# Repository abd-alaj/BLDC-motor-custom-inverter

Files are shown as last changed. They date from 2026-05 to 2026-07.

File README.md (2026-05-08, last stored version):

Hello, 

this is the start of our casptone project. 

You will see the following structure (with changes if i have forgotten to update this section):  

```
.
├── data/                    - parameters, csv files, oscilloscope data
├── docs/                    - documentation of our project
├── hardware/                - KiCad Project files, scheamtic, footprints, etc.
│   ├── schematics/             - schematic files
│   ├── layout/                 - PCB layout files
│   ├── libraries/              - custom footprints/symbols
│   └── manufacturing/          - gerbers, BOM, etc.
├── models/                 - main simulink directory
│   └── components/              - smaller components for the model
├── scripts/                 - utility matlab scripts
├── src/                     - C code
└── work/                    - MATLAB throws autogenerated files in here 
```

# How To Use This Code
1. git clone this repo: 
```
git clone https://github.com/abd-alaj/BLDC-motor-custom-inverter.git
```
2. open the `BLDC_motor_custom_inverter.m.prj` file in matlab prior to starting any work.

That's it. This project is in a rather primitive state so this readme file is an active WIP.

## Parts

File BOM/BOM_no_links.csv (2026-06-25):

Reference | Qty | Value | DNP | Exclude from BOM | Exclude from Board | Footprint | Datasheet
C1,C2,C3,C6,C7,C8,C10,C11,C12,C13,C14,C15,C16,C17,C18,C19,C20,C21,C22,C26,C27 | 21 | 100n |  |  |  | Capacitor_SMD:C_0603_1608Metric
C4,C5,C9 | 3 | 4.7u |  |  |  | Capacitor_SMD:C_0603_1608Metric
C28,C29 | 2 | 330u |  |  |  | footprint:PCAP_12_5x20-THRU-ELECT_NCA
C30,C31 | 2 | 1u |  |  |  | Capacitor_SMD:C_0603_1608Metric
C32,C33,C34,C35,C36,C37 | 6 | 10u |  |  |  | Capacitor_SMD:C_0805_2012Metric
CR1,CR3 | 2 | SMCJ26 |  |  |  | footprint:SMCJSeries_LTF | SMCJ26
D1,D2,D3 | 3 | MURA160T3G |  |  |  | footprint:MURA160T3G
D4,D6 | 2 | MM5Z10VT1G |  |  |  | Diode_SMD:D_SOD-523 | https://diotec.com/tl_files/diotec/files/pdf/datasheets/mm5z2v4.pdf
D5 | 1 | SS14 |  |  |  | Diode_SMD:D_SMA | https://www.vishay.com/docs/88746/ss12.pdf
D7,D8,D9,D10 | 4 | LED |  |  |  | LED_SMD:LED_0603_1608Metric
J1 | 1 | Screw_Terminal_01x03 |  |  |  | TerminalBlock_Phoenix:TerminalBlock_Phoenix_MKDS-1,5-3-5.08_1x03_P5.08mm_Horizontal
J2,J3,J4 | 3 | Screw_Terminal_01x02 |  |  |  | TerminalBlock_Phoenix:TerminalBlock_Phoenix_MKDS-1,5-2-5.08_1x02_P5.08mm_Horizontal
J5 | 1 | Conn_01x08_Pin |  |  |  | Connector_JST:JST_XH_B8B-XH-A_1x08_P2.50mm_Vertical
Q1,Q2,Q3,Q4,Q5,Q6 | 6 | IRLZ44N |  |  |  | Package_TO_SOT_THT:TO-220-3_Vertical | http://www.irf.com/product-info/datasheets/data/irlz44n.pdf
Q7,Q9 | 2 | DMP6050SSD |  |  |  | Package_SO:SOIC-8_3.9x4.9mm_P1.27mm | https://www.diodes.com/assets/Datasheets/DMP6050SSD.pdf
R1,R2,R3,R6,R7,R8,R10,R11,R12 | 9 | 10 |  |  |  | Resistor_SMD:R_0603_1608Metric
R4,R17 | 2 | 47k |  |  |  | Resistor_SMD:R_0603_1608Metric
R5,R9,R16 | 3 | 4.7k |  |  |  | Resistor_SMD:R_0603_1608Metric
R13,R14,R15 | 3 | 10m |  |  |  | Resistor_SMD:R_2512_6332Metric
R18,R19,R20,R28 | 4 | 3.3k |  |  |  | Resistor_SMD:R_0603_1608Metric
R21,R22,R30,R31,R32,R33,R34,R35,R36,R37,R38,R39,R40,R41,R42 | 15 | 0 |  |  |  | Resistor_SMD:R_0402_1005Metric
R23,R24,R27 | 3 | 680 |  |  |  | Resistor_SMD:R_0603_1608Metric
R25,R26 | 2 | 10k |  |  |  | Resistor_SMD:R_0603_1608Metric
R29 | 1 | 33k |  |  |  | Resistor_SMD:R_0603_1608Metric
R43 | 1 | 680 |  |  |  | Resistor_SMD:R_0603_1608Metric_Pad0.98x0.95mm_HandSolder
R44 | 1 | 100 |  |  |  | Resistor_SMD:R_0603_1608Metric_Pad0.98x0.95mm_HandSolder
R45 | 1 | 6.98k |  |  |  | Resistor_SMD:R_1206_3216Metric_Pad1.30x1.75mm_HandSolder
R46 | 1 | 3k |  |  |  | Resistor_SMD:R_0805_2012Metric_Pad1.20x1.40mm_HandSolder
RV1 | 1 | 10k |  |  |  | Potentiometer_THT:Potentiometer_Alps_RK09K_Single_Vertical
TP1,TP2,TP3,TP4,TP5,TP6,TP7,TP8,TP9,TP10,TP11,TP12,TP13,TP14,TP15,TP16,TP17,TP18,TP20,TP24 | 20 | TestPoint |  |  |  | TestPoint:TestPoint_Pad_1.5x1.5mm
TP21,TP22,TP23 | 3 | Keystone 5015 |  |  |  | TestPoint:TestPoint_Keystone_5015_Micro_Mini
U1 | 1 | NUCLEO64-F411RE |  |  |  | Module:ST_Morpho_Connector_144_STLink | http://www.st.com/st-web-ui/static/active/en/resource/technical/document/data_brief/DM00105918.pdf
U2,U3,U4 | 3 | INA181 |  |  |  | Package_TO_SOT_SMD:SOT-23-6 | http://www.ti.com/lit/ds/symlink/ina181.pdf
U5,U6,U7 | 3 | ADUM3223ARZ |  |  |  | footprint:SOIC127P600X175-16N
U8 | 1 | LMV321 |  |  |  | footprint:LMV321DBV5 | http://www.ti.com/lit/ds/symlink/lmv324.pdf
U9,U10,U11 | 3 | TL331 |  |  |  | Package_TO_SOT_SMD:SOT-23-5 | http://www.ti.com/lit/ds/symlink/tl331.pdf
U12 | 1 | AP2112K-2.6 |  |  |  | Package_TO_SOT_SMD:SOT-23-5 | https://www.diodes.com/assets/Datasheets/AP2112.pdf
U13 | 1 | 74LVC1G332 |  |  |  | footprint:MURA160T3G | http://www.ti.com/lit/sg/scyt129e/scyt129e.pdf

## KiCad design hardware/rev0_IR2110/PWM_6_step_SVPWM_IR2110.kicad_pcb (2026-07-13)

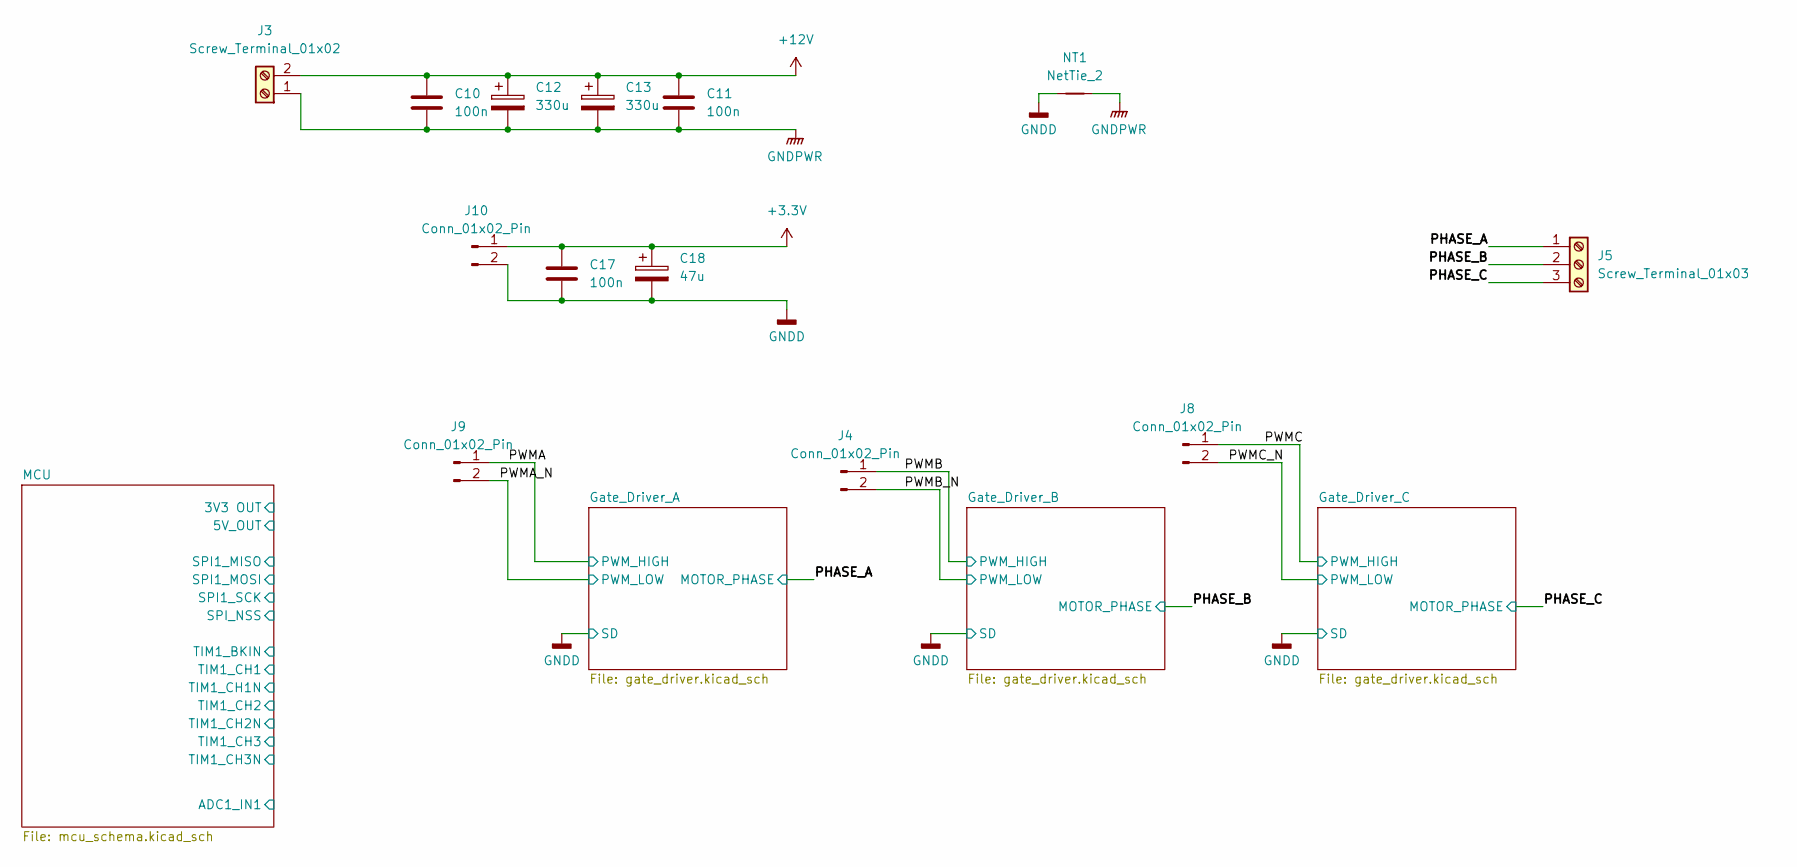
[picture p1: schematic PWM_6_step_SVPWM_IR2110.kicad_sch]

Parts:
C10, C11, C17: 100n; C_1206_3216Metric
C12, C13: 330u; PCAP_12_5x20-THRU-ELECT_NCA
C18: 47u; CP_Radial_D8.0mm_P3.50mm
J3: Screw_Terminal_01x02; TerminalBlock_TE_282834-2_1x02_P2.54mm_Horizontal
J4, J8, J9, J10: Conn_01x02_Pin; PinHeader_1x02_P2.54mm_Vertical
J5: Screw_Terminal_01x03; TerminalBlock_TE_282834-3_1x03_P2.54mm_Horizontal
NT1: NetTie_2; NetTie-2_SMD_Pad2.0mm

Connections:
+3.3V: C17.1, C18.1, J10.1; also elsewhere on the board
+12V: C10.1, C11.1, C12.1, C13.1, J3.2; also elsewhere on the board
/PHASE_A: J5.1; also elsewhere on the board
/PHASE_B: J5.2; also elsewhere on the board
/PHASE_C: J5.3; also elsewhere on the board
/PWMA: J9.1; also elsewhere on the board
/PWMA_N: J9.2; also elsewhere on the board
/PWMB: J4.1; also elsewhere on the board
/PWMB_N: J4.2; also elsewhere on the board
/PWMC: J8.1; also elsewhere on the board
/PWMC_N: J8.2; also elsewhere on the board
GNDD: C17.2, C18.2, J10.2, NT1.1; also elsewhere on the board
GNDPWR: C10.2, C11.2, C12.2, C13.2, J3.1, NT1.2; also elsewhere on the board

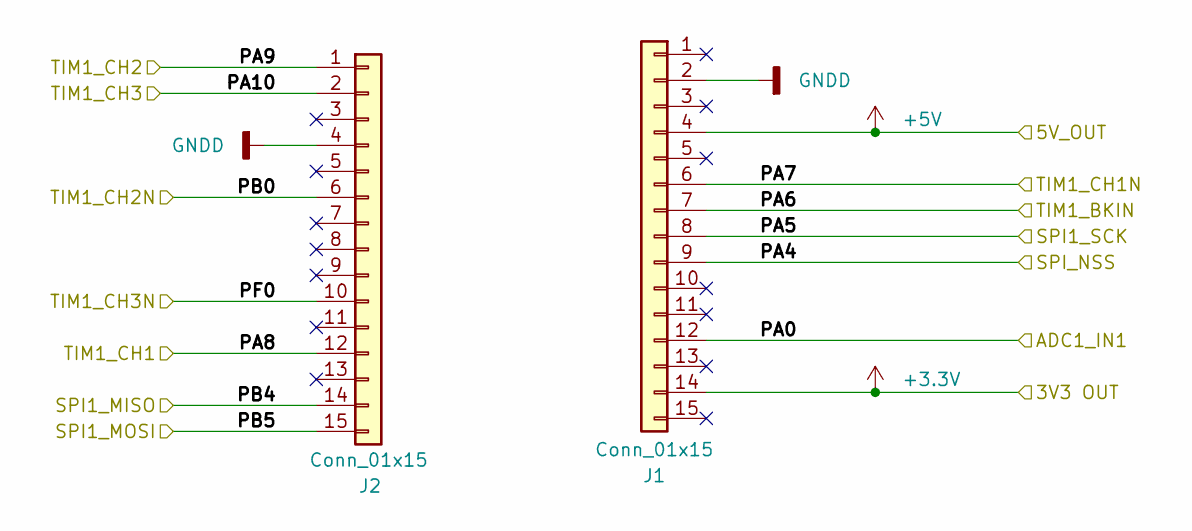
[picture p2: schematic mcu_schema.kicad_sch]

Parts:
J1, J2: Conn_01x15; PinSocket_1x15_P2.54mm_Vertical

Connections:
unnamed: J1.2, J2.4

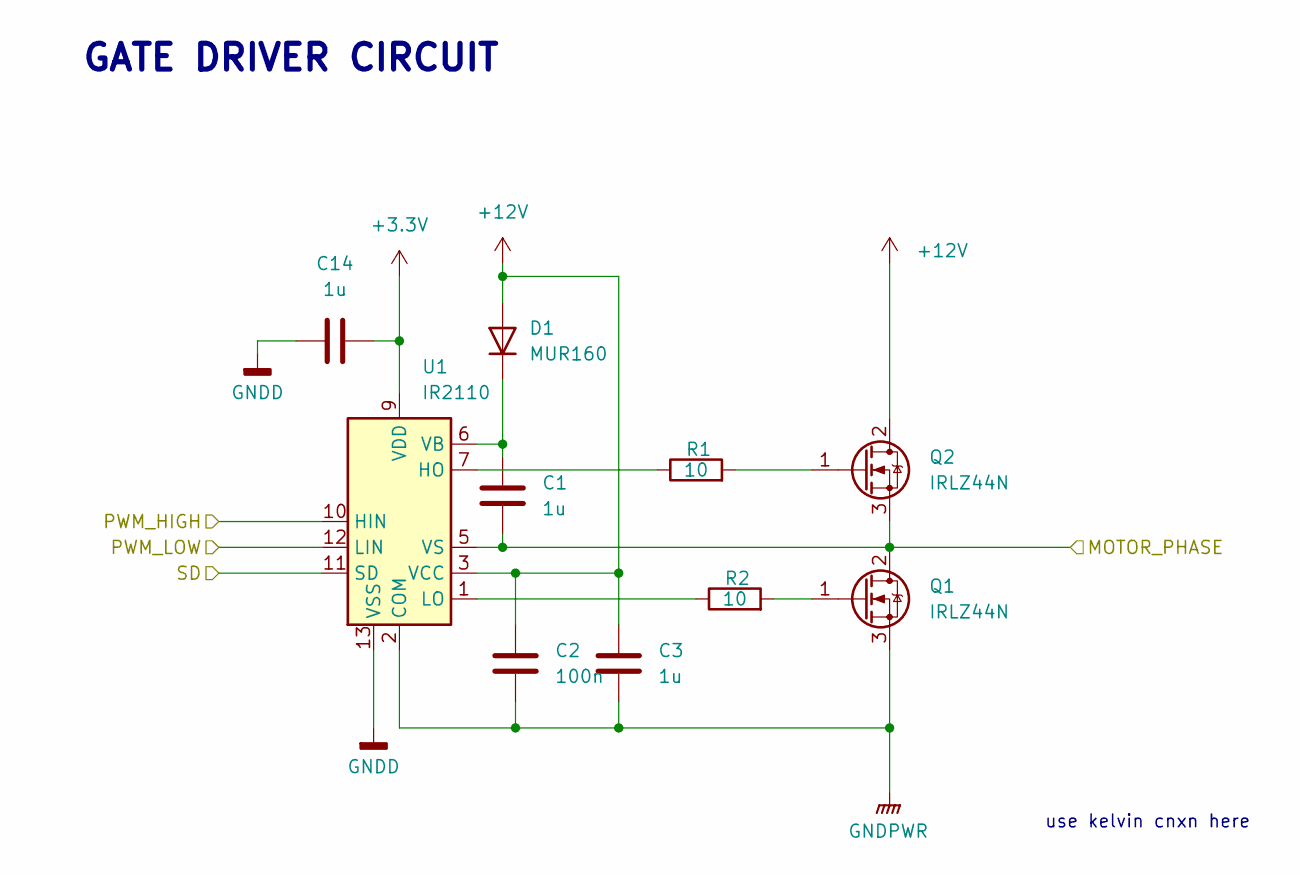
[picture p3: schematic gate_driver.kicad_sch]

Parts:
C1, C3: 1u; C_1206_3216Metric
C2: 100n; C_1206_3216Metric
C14: 1u; C_0603_1608Metric
D1: MUR160; D_DO-41_SOD81_P10.16mm_Horizontal
Q1, Q2: IRLZ44N; TO-220-3_Vertical
R1, R2: 10; R_1206_3216Metric
U1: IR2110; DIP-14_W7.62mm

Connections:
+3.3V: C14.2, U1.9 (VDD); also elsewhere on the board
+12V: C2.1, C3.1, D1.2 (A), Q2.2 (D), U1.3 (VCC); also elsewhere on the board
/PHASE_A: C1.2, Q1.2 (D), Q2.3 (S), U1.5 (VS); also elsewhere on the board
/PWMA: U1.10 (HIN); also elsewhere on the board
/PWMA_N: U1.12 (LIN); also elsewhere on the board
GNDD: C14.1, U1.11 (SD), U1.13 (VSS); also elsewhere on the board
GNDPWR: C2.2, C3.2, Q1.3 (S), U1.2 (COM); also elsewhere on the board
unnamed: C1.1, D1.1 (K), U1.6 (VB)
unnamed: Q1.1 (G), R2.2
unnamed: Q2.1 (G), R1.2
unnamed: R1.1, U1.7 (HO)
unnamed: R2.1, U1.1 (LO)

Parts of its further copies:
C4, C6, C7, C9: 1u; C_1206_3216Metric
C5, C8: 100n; C_1206_3216Metric
C15, C16: 1u; C_0603_1608Metric
D2, D3: MUR160; D_DO-41_SOD81_P10.16mm_Horizontal
Q3, Q4, Q5, Q6: IRLZ44N; TO-220-3_Vertical
R3, R4, R5, R6: 10; R_1206_3216Metric
U2, U3: IR2110; DIP-14_W7.62mm

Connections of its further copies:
+3.3V: C15.2, C16.2, U2.9 (VDD), U3.9 (VDD); also elsewhere on the board
+12V: C5.1, C6.1, C8.1, C9.1, D2.2 (A), D3.2 (A), Q3.2 (D), Q5.2 (D), U2.3 (VCC), U3.3 (VCC); also elsewhere on the board
/PHASE_B: C4.2, Q3.3 (S), Q4.2 (D), U2.5 (VS); also elsewhere on the board
/PHASE_C: C7.2, Q5.3 (S), Q6.2 (D), U3.5 (VS); also elsewhere on the board
/PWMB: U2.10 (HIN); also elsewhere on the board
/PWMB_N: U2.12 (LIN); also elsewhere on the board
/PWMC: U3.10 (HIN); also elsewhere on the board
/PWMC_N: U3.12 (LIN); also elsewhere on the board
GNDD: C15.1, C16.1, U2.11 (SD), U2.13 (VSS), U3.11 (SD), U3.13 (VSS); also elsewhere on the board
GNDPWR: C5.2, C6.2, C8.2, C9.2, Q4.3 (S), Q6.3 (S), U2.2 (COM), U3.2 (COM); also elsewhere on the board
unnamed: C4.1, D2.1 (K), U2.6 (VB)
unnamed: C7.1, D3.1 (K), U3.6 (VB)
unnamed: Q3.1 (G), R3.2
unnamed: Q4.1 (G), R4.2
unnamed: Q5.1 (G), R5.2
unnamed: Q6.1 (G), R6.2
unnamed: R3.1, U2.7 (HO)
unnamed: R4.1, U2.1 (LO)
unnamed: R5.1, U3.7 (HO)
unnamed: R6.1, U3.1 (LO)

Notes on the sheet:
GATE DRIVER CIRCUIT
use kelvin cnxn here

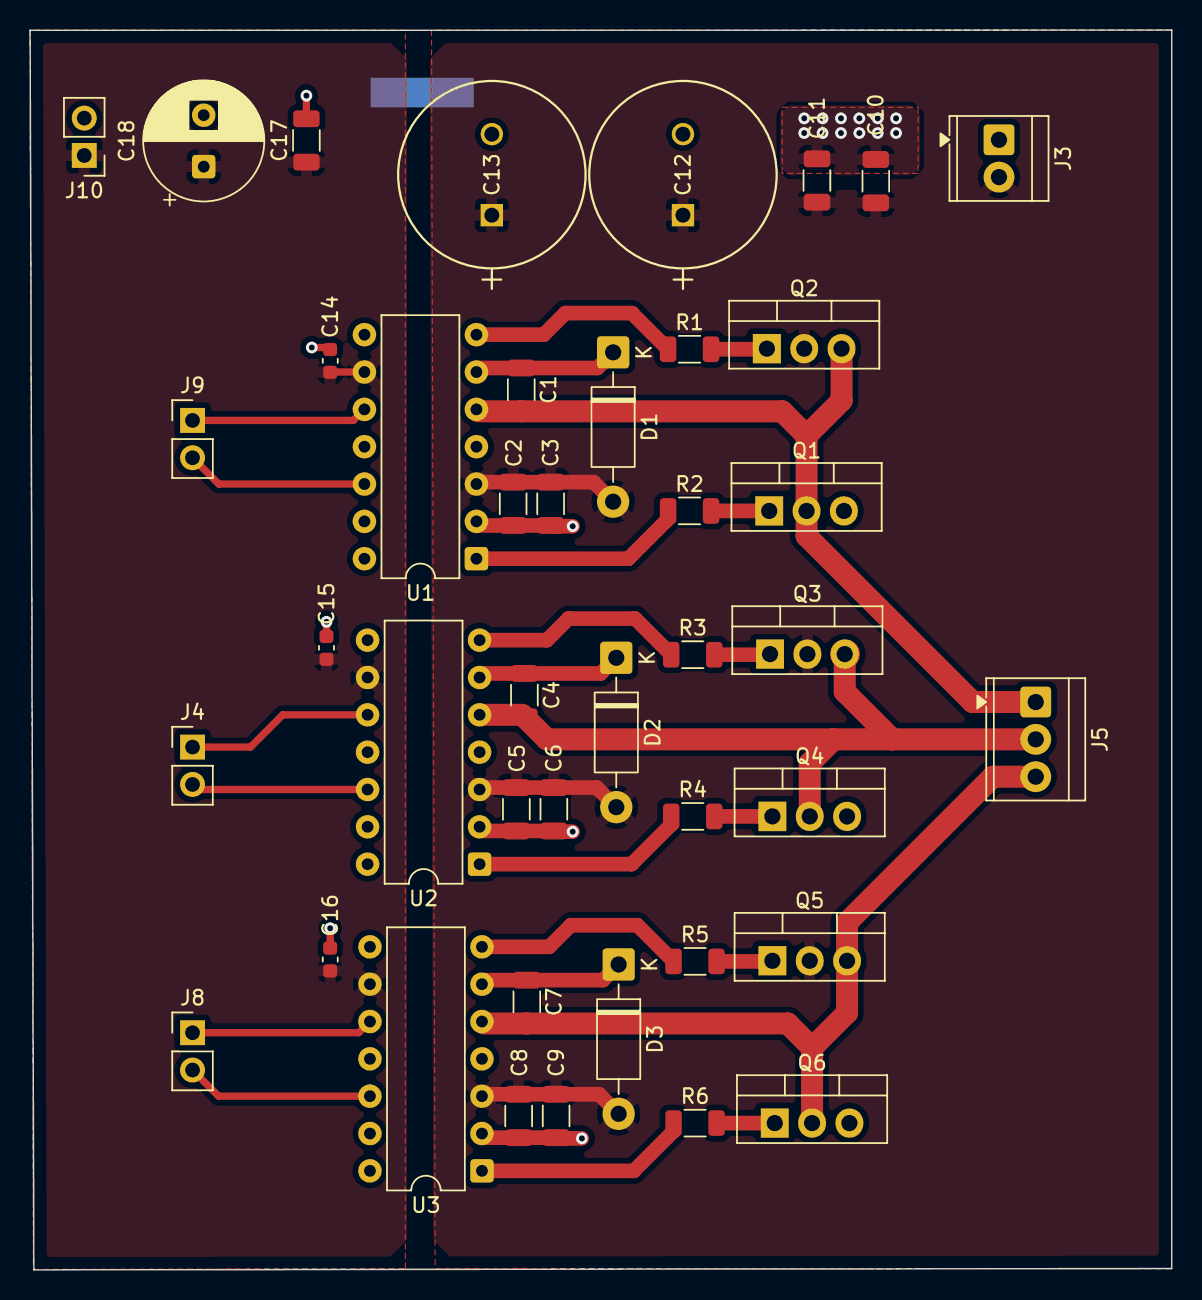
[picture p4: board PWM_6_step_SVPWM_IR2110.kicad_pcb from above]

Board: 2 copper layers, 77.7 x 84.3 mm, 43 parts (1 on the bottom side), 28 nets.

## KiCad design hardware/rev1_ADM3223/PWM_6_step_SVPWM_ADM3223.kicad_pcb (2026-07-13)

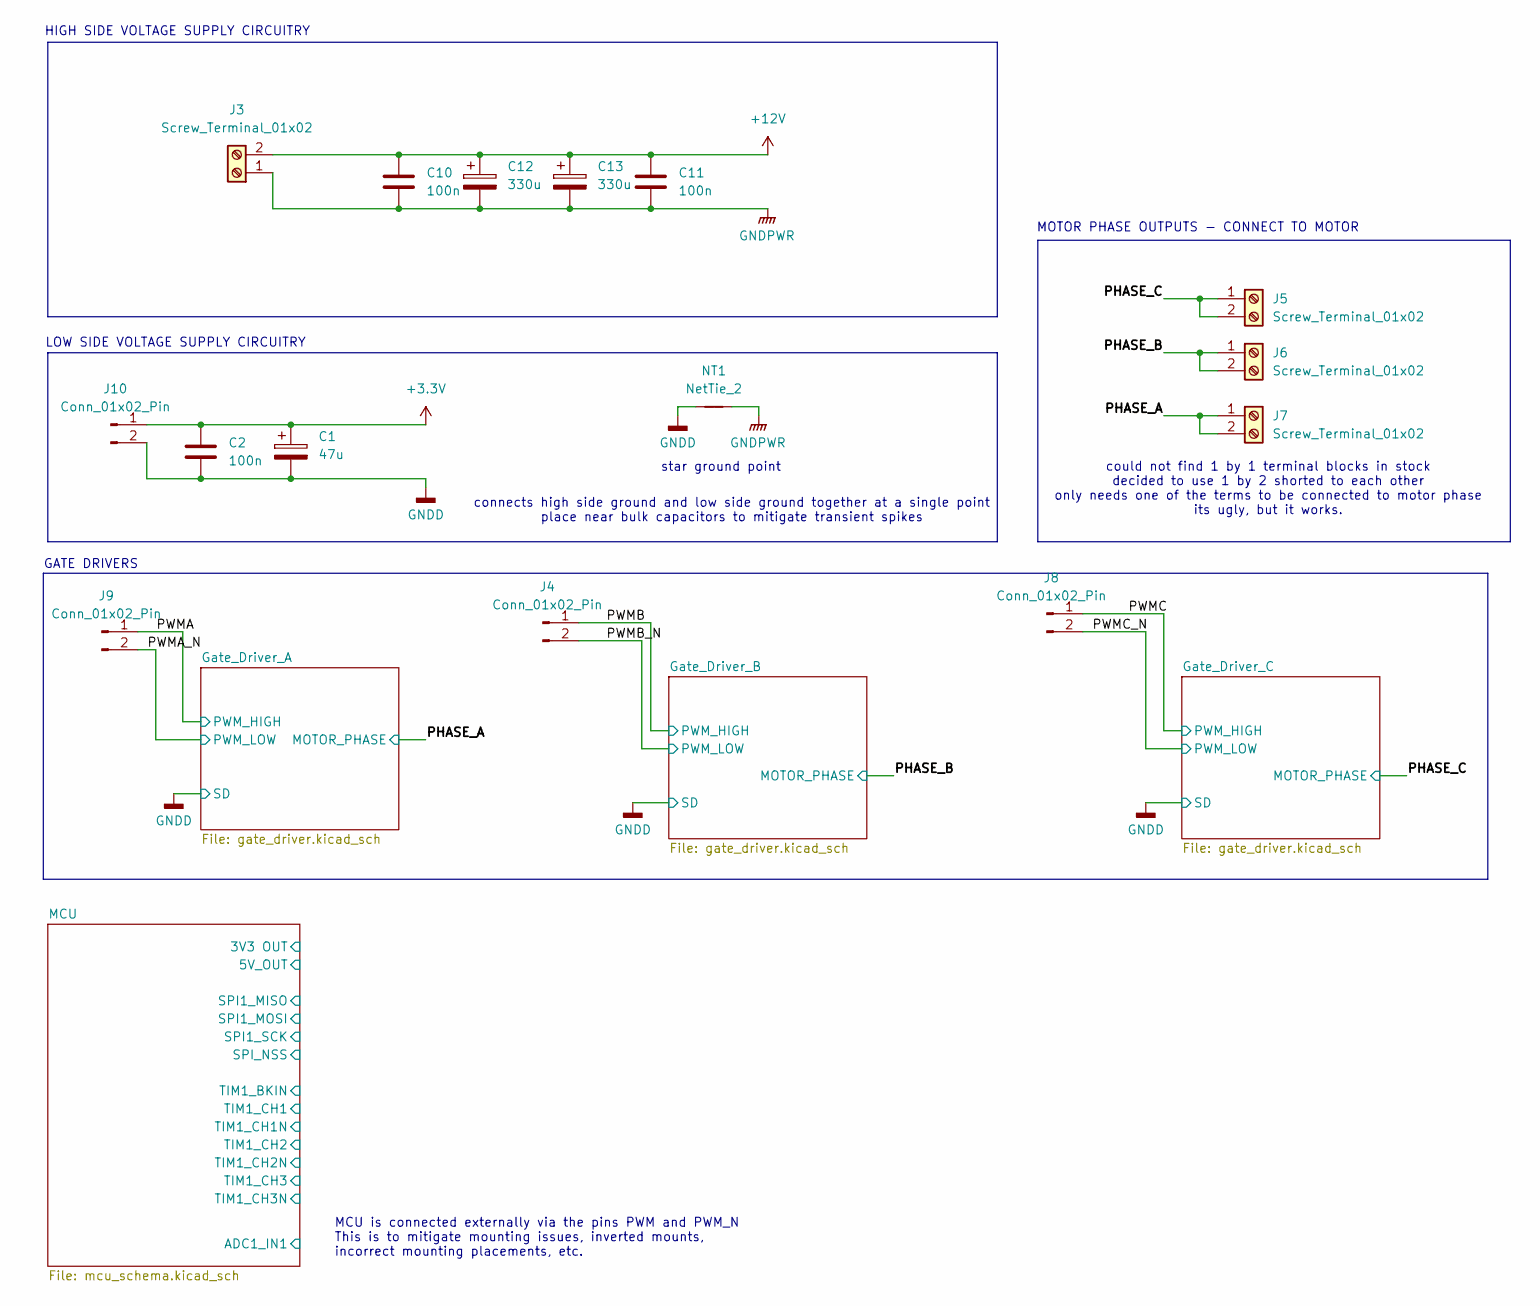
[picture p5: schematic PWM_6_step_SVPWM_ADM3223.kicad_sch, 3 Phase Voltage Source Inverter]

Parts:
C1: 47u; CP_Radial_D8.0mm_P3.50mm
C2, C10, C11: 100n; C_1206_3216Metric
C12, C13: 330u; PCAP_12_5x20-THRU-ELECT_NCA
J3, J5, J6, J7: Screw_Terminal_01x02; TerminalBlock_TE_282834-2_1x02_P2.54mm_Horizontal
J4, J8, J9, J10: Conn_01x02_Pin; PinHeader_1x02_P2.54mm_Vertical
NT1: NetTie_2; NetTie-2_SMD_Pad2.0mm

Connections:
+3.3V: C1.1, C2.1, J10.1; also elsewhere on the board
+12V: C10.1, C11.1, C12.1, C13.1, J3.2; also elsewhere on the board
/PHASE_A: J7.1, J7.2; also elsewhere on the board
/PHASE_B: J6.1, J6.2; also elsewhere on the board
/PHASE_C: J5.1, J5.2; also elsewhere on the board
/PWMA: J9.1; also elsewhere on the board
/PWMA_N: J9.2; also elsewhere on the board
/PWMB: J4.1; also elsewhere on the board
/PWMB_N: J4.2; also elsewhere on the board
/PWMC: J8.1; also elsewhere on the board
/PWMC_N: J8.2; also elsewhere on the board
GNDD: C1.2, C2.2, J10.2, NT1.1; also elsewhere on the board
GNDPWR: C10.2, C11.2, C12.2, C13.2, J3.1, NT1.2; also elsewhere on the board

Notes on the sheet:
HIGH SIDE VOLTAGE SUPPLY CIRCUITRY
star ground point
MOTOR PHASE OUTPUTS - CONNECT TO MOTOR
connects high side ground and low side ground together at a single point place near bulk capacitors to mitigate transient spikes
LOW SIDE VOLTAGE SUPPLY CIRCUITRY
MCU is connected externally via the pins PWM and PWM_N This is to mitigate mounting issues, inverted mounts, incorrect mounting placements, etc.
GATE DRIVERS
could not find 1 by 1 terminal blocks in stock decided to use 1 by 2 shorted to each other only needs one of the terms to be connected to motor phase its ugly, but it works.


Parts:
J1, J2: Conn_01x15; PinSocket_1x15_P2.54mm_Vertical

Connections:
unnamed: J1.2, J2.4

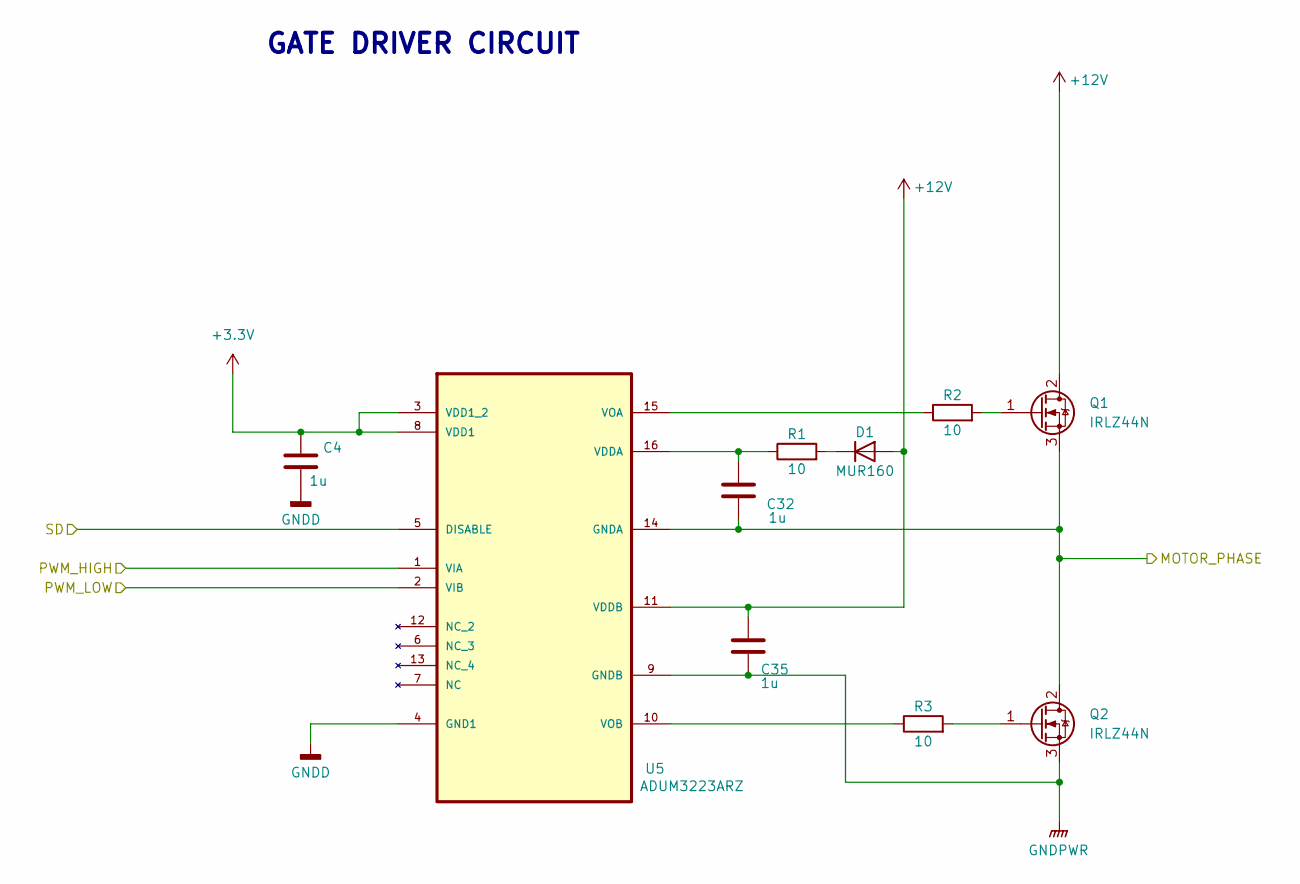
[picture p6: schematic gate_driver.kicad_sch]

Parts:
C4, C32, C35: 1u; C_0603_1608Metric
D1: MUR160; D_DO-41_SOD81_P7.62mm_Horizontal
Q1, Q2: IRLZ44N; TO-220-3_Vertical
R1, R2, R3: 10; R_1206_3216Metric
U5: ADUM3223ARZ; SOIC127P600X175-16N; MPN ADUM3223ARZ

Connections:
+3.3V: C4.1, U5.3 (VDD1_2), U5.8 (VDD1); also elsewhere on the board
+12V: C35.1, D1.2 (A), Q1.2 (D), U5.11 (VDDB); also elsewhere on the board
/PHASE_A: C32.2, Q1.3 (S), Q2.2 (D), U5.14 (GNDA); also elsewhere on the board
/PWMA: U5.1 (VIA); also elsewhere on the board
/PWMA_N: U5.2 (VIB); also elsewhere on the board
GNDD: C4.2, U5.4 (GND1), U5.5 (DISABLE); also elsewhere on the board
GNDPWR: C35.2, Q2.3 (S), U5.9 (GNDB); also elsewhere on the board
unnamed: D1.1 (K), R1.2
unnamed: Q1.1 (G), R2.2
unnamed: Q2.1 (G), R3.2
unnamed: C32.1, R1.1, U5.16 (VDDA)
unnamed: R2.1, U5.15 (VOA)
unnamed: R3.1, U5.10 (VOB)

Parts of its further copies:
C5, C9, C33, C34, C36, C37: 1u; C_0603_1608Metric
D2, D3: MUR160; D_DO-41_SOD81_P7.62mm_Horizontal
Q3, Q4, Q5, Q6: IRLZ44N; TO-220-3_Vertical
R4, R5, R6, R7, R8, R9: 10; R_1206_3216Metric
U6, U7: ADUM3223ARZ; SOIC127P600X175-16N; MPN ADUM3223ARZ

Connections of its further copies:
+3.3V: C5.1, C9.1, U6.3 (VDD1_2), U6.8 (VDD1), U7.3 (VDD1_2), U7.8 (VDD1); also elsewhere on the board
+12V: C36.1, C37.1, D2.2 (A), D3.2 (A), Q3.2 (D), Q5.2 (D), U6.11 (VDDB), U7.11 (VDDB); also elsewhere on the board
/PHASE_B: C33.2, Q3.3 (S), Q4.2 (D), U6.14 (GNDA); also elsewhere on the board
/PHASE_C: C34.2, Q5.3 (S), Q6.2 (D), U7.14 (GNDA); also elsewhere on the board
/PWMB: U6.1 (VIA); also elsewhere on the board
/PWMB_N: U6.2 (VIB); also elsewhere on the board
/PWMC: U7.1 (VIA); also elsewhere on the board
/PWMC_N: U7.2 (VIB); also elsewhere on the board
GNDD: C5.2, C9.2, U6.4 (GND1), U6.5 (DISABLE), U7.4 (GND1), U7.5 (DISABLE); also elsewhere on the board
GNDPWR: C36.2, C37.2, Q4.3 (S), Q6.3 (S), U6.9 (GNDB), U7.9 (GNDB); also elsewhere on the board
unnamed: D2.1 (K), R4.2
unnamed: D3.1 (K), R7.2
unnamed: Q3.1 (G), R6.2
unnamed: Q4.1 (G), R5.2
unnamed: Q5.1 (G), R9.2
unnamed: Q6.1 (G), R8.2
unnamed: C33.1, R4.1, U6.16 (VDDA)
unnamed: R6.1, U6.15 (VOA)
unnamed: R5.1, U6.10 (VOB)
unnamed: C34.1, R7.1, U7.16 (VDDA)
unnamed: R9.1, U7.15 (VOA)
unnamed: R8.1, U7.10 (VOB)

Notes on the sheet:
GATE DRIVER CIRCUIT

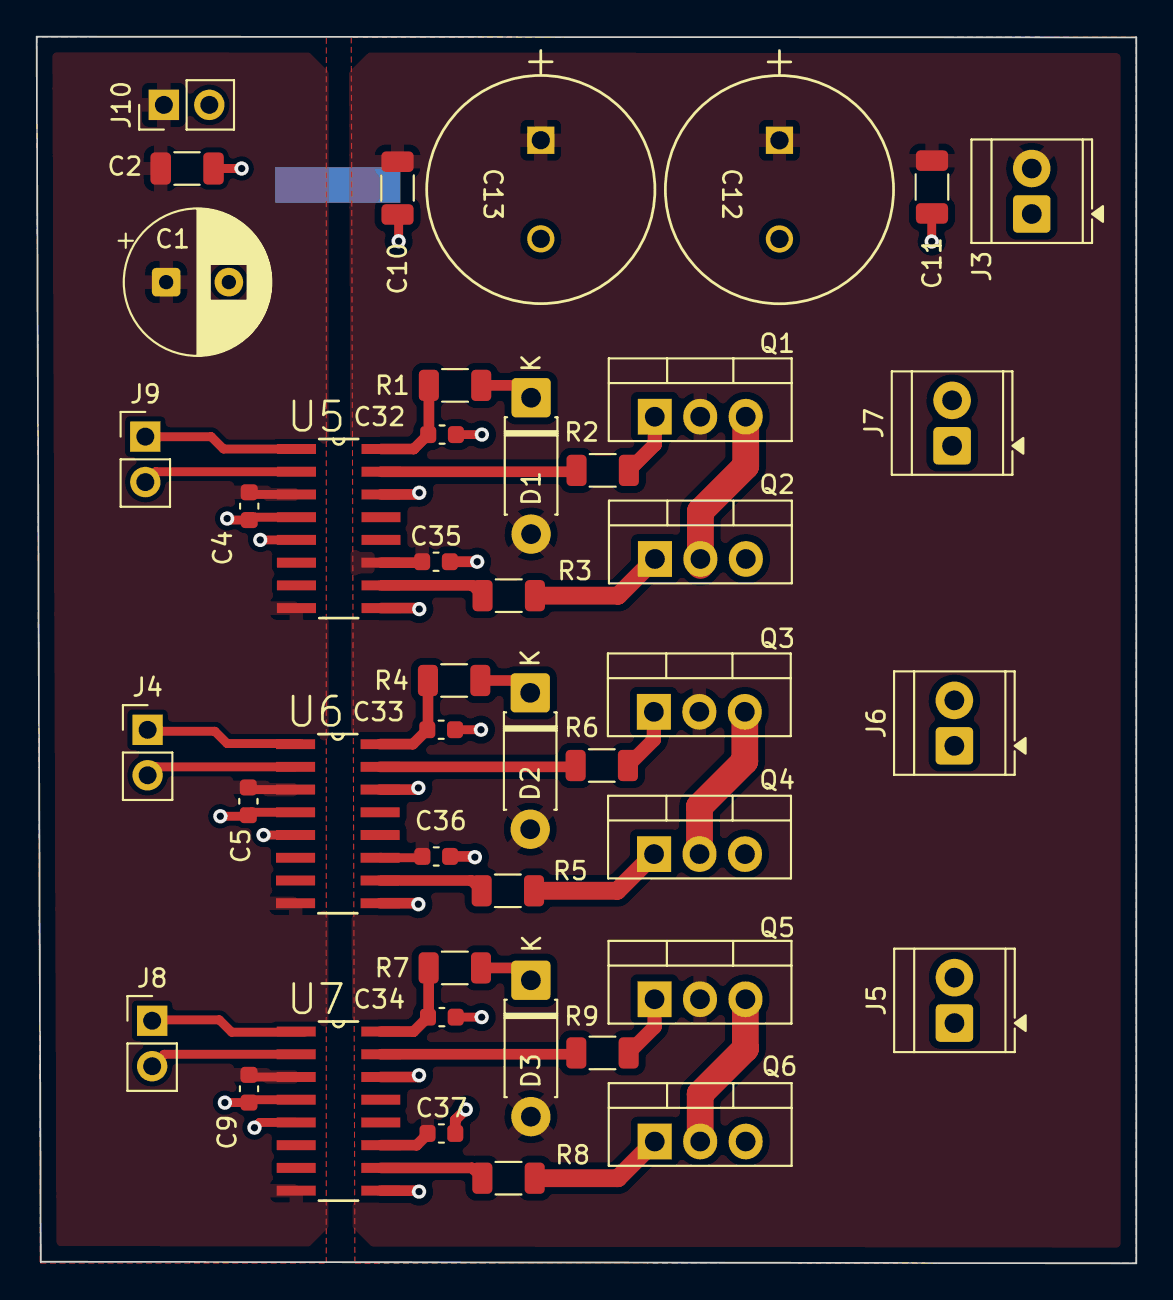
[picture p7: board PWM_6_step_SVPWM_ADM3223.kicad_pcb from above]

Board: 2 copper layers, 61.4 x 68.5 mm, 45 parts (1 on the bottom side), 31 nets.

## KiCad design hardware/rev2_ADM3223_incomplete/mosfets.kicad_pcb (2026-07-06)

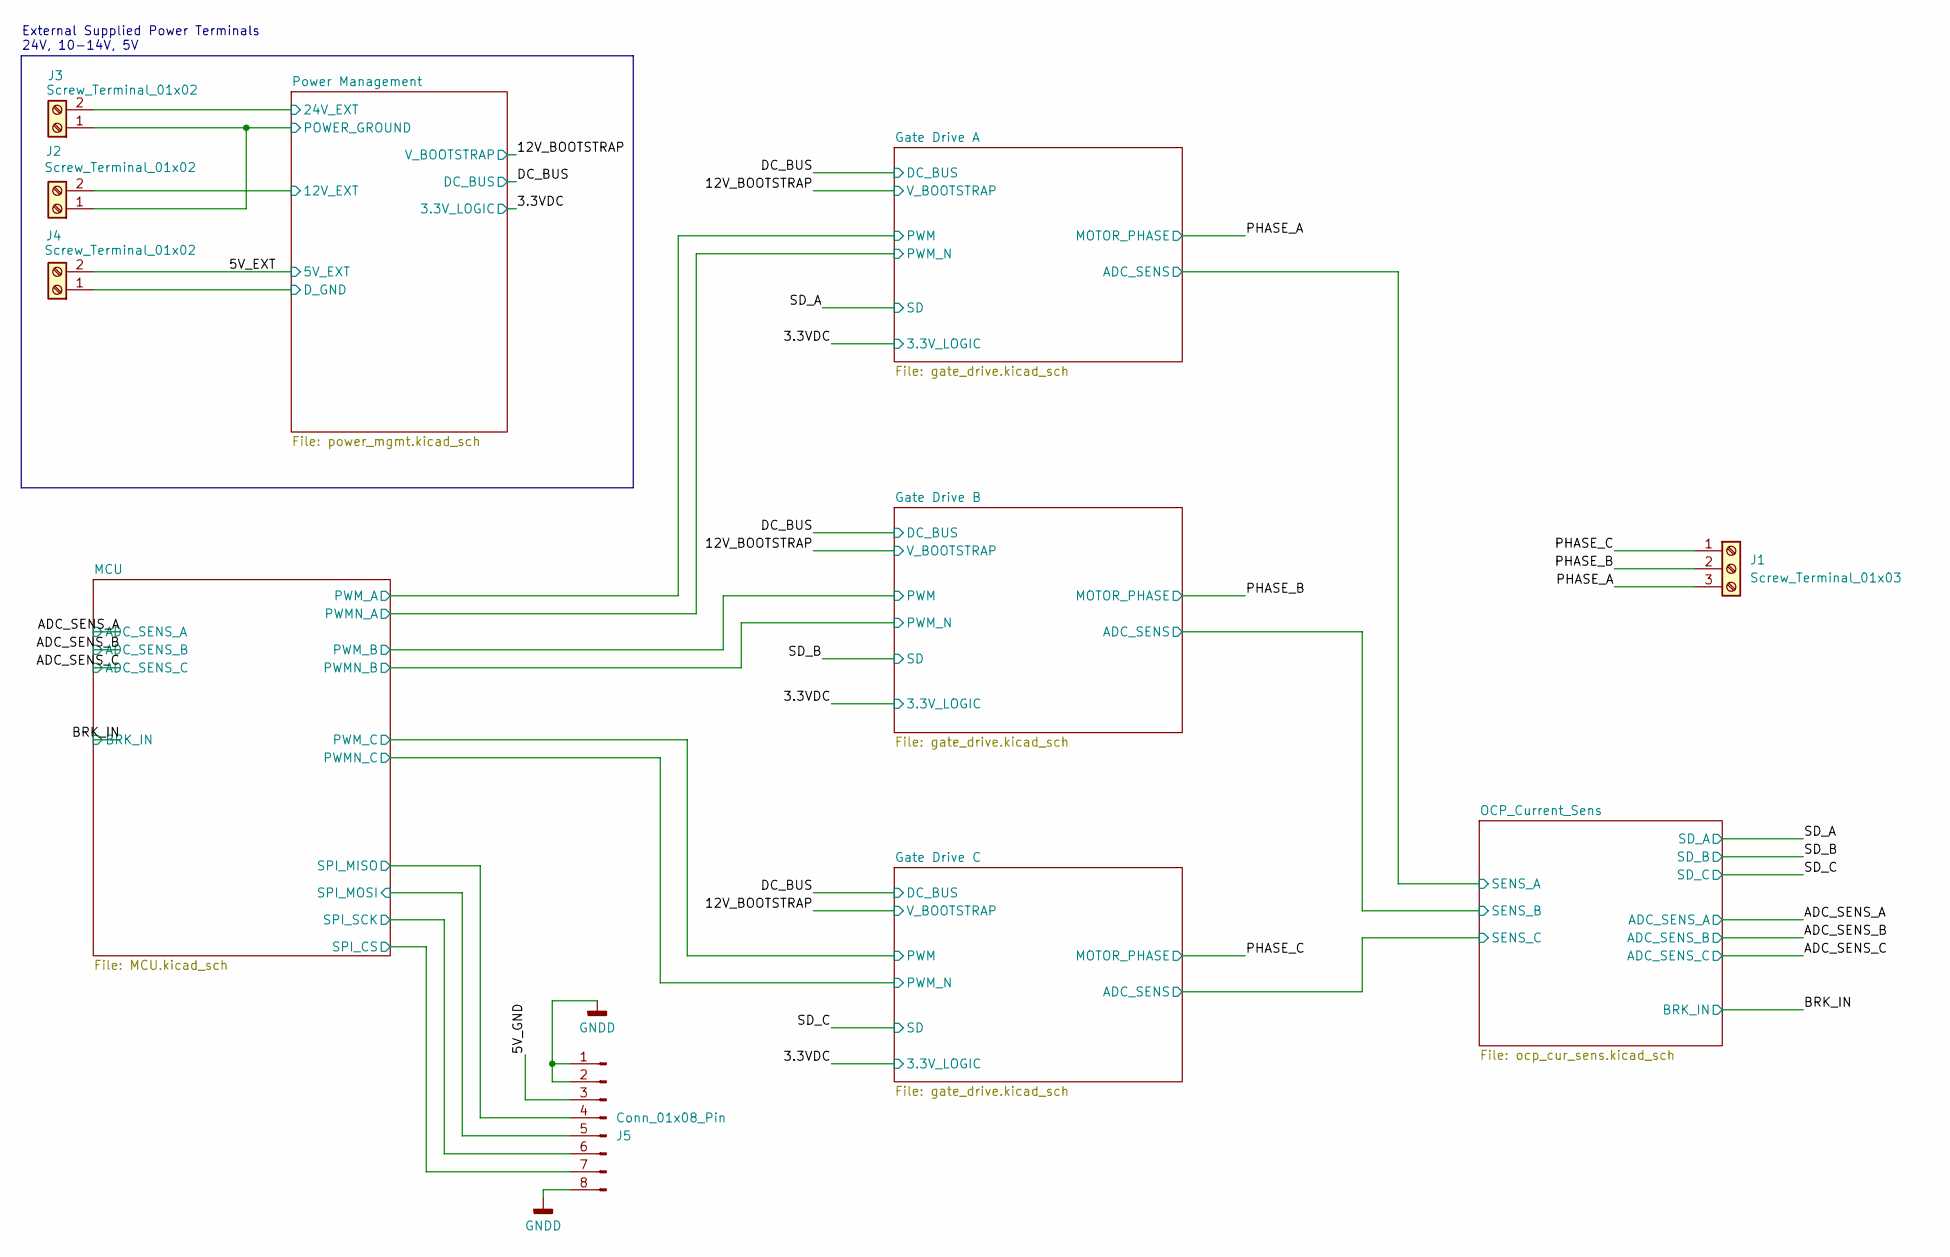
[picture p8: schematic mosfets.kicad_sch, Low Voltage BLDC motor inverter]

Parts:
J1: Screw_Terminal_01x03; TerminalBlock_Phoenix_MKDS-1,5-3-5.08_1x03_P5.08mm_Horizont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
J2, J3, J4: Screw_Terminal_01x02; TerminalBlock_Phoenix_MKDS-1,5-2-5.08_1x02_P5.08mm_Horizont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
J5: Conn_01x08_Pin; JST_XH_B8B-XH-A_1x08_P2.50mm_Vertical

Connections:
+5V: J4.2; also elsewhere on the board
/5V_GND: J5.3
/MCU/SPI_CS: J5.7; also elsewhere on the board
/MCU/SPI_MISO: J5.4; also elsewhere on the board
/MCU/SPI_MOSI: J5.5; also elsewhere on the board
/MCU/SPI_SCK: J5.6; also elsewhere on the board
/PHASE_A: J1.3; also elsewhere on the board
/PHASE_B: J1.2; also elsewhere on the board
/PHASE_C: J1.1; also elsewhere on the board
/Power Management/12V_EXT: J2.2; also elsewhere on the board
/Power Management/24V_EXT: J3.2; also elsewhere on the board
GNDA: J4.1, J5.1, J5.2, J5.8; also elsewhere on the board
GNDPWR: J2.1, J3.1; also elsewhere on the board

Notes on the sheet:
External Supplied Power Terminals 24V, 10-14V, 5V

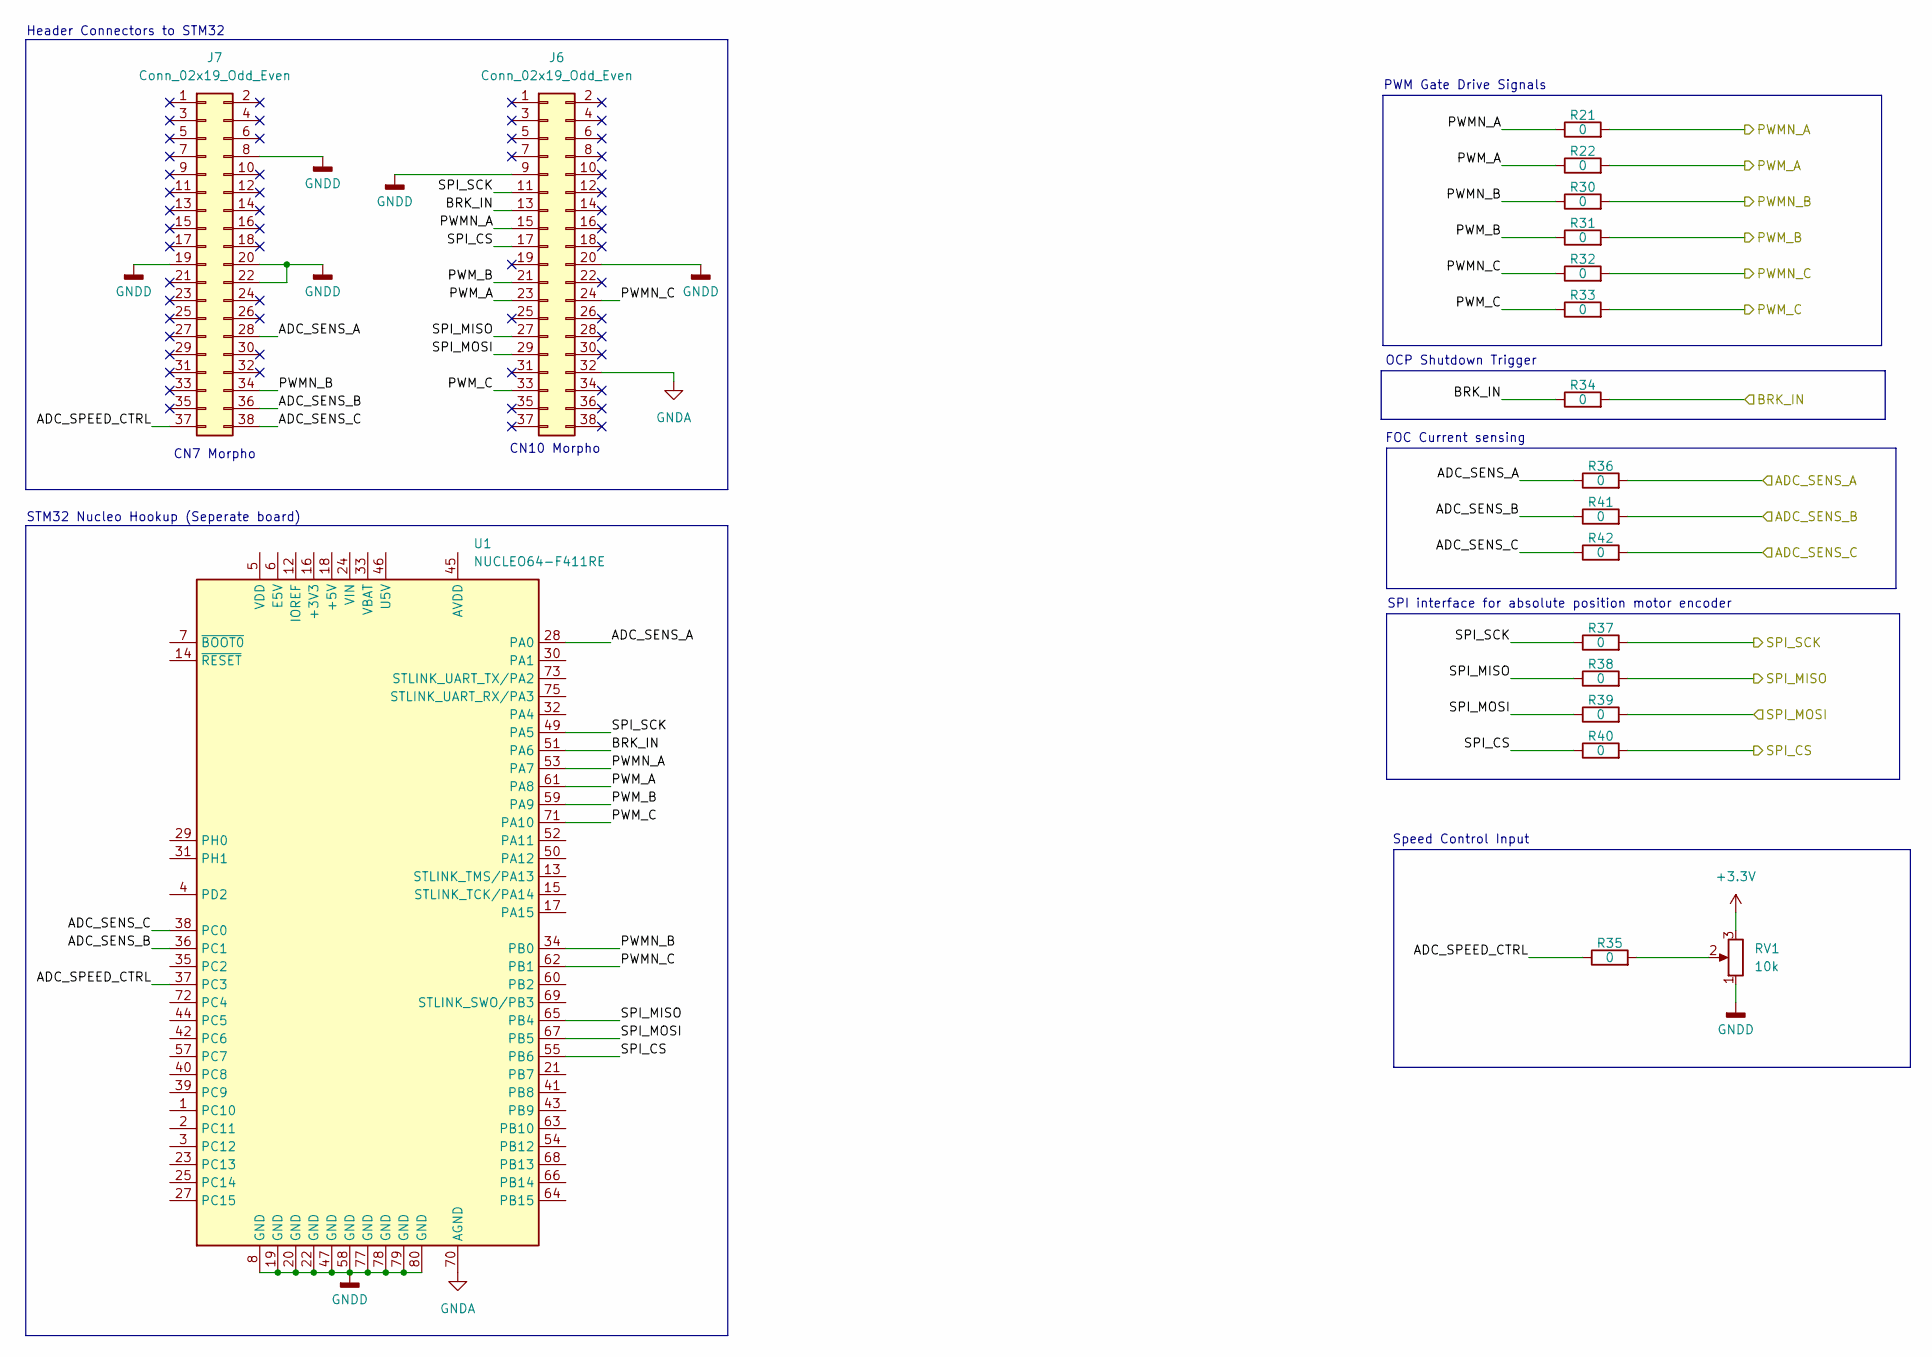
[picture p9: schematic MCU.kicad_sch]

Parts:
J6, J7: Conn_02x19_Odd_Even; PinSocket_2x19_P2.54mm_Vertical
R21, R22, R30, R31, R32, R33, R34, R35, R36, R37, R38, R39, R40, R41, R42: 0; R_0402_1005Metric
RV1: 10k; Potentiometer_Alps_RK09K_Single_Vertical
U1: NUCLEO64-F411RE; ST_Morpho_Connector_144_STLink

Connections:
+3.3V: RV1.3; also elsewhere on the board
/ADC_SENS_A: J7.28, R36.1, R36.2, U1.28 (PA0); also elsewhere on the board
/ADC_SENS_B: J7.36, R41.1, R41.2, U1.36 (PC1); also elsewhere on the board
/ADC_SENS_C: J7.38, R42.1, R42.2, U1.38 (PC0); also elsewhere on the board
/BRK_IN: J6.13, R34.1, R34.2, U1.51 (PA6); also elsewhere on the board
/MCU/ADC_SPEED_CTRL: J7.37, R35.1, U1.37 (PC3)
/MCU/PWMN_A: J6.15, R21.1, R21.2, U1.53 (PA7); also elsewhere on the board
/MCU/PWMN_B: J7.34, R30.1, R30.2, U1.34 (PB0); also elsewhere on the board
/MCU/PWMN_C: J6.24, R32.1, R32.2, U1.62 (PB1); also elsewhere on the board
/MCU/PWM_A: J6.23, R22.1, R22.2, U1.61 (PA8); also elsewhere on the board
/MCU/PWM_B: J6.21, R31.1, R31.2, U1.59 (PA9); also elsewhere on the board
/MCU/PWM_C: J6.33, R33.1, R33.2, U1.71 (PA10); also elsewhere on the board
/MCU/SPI_CS: J6.17, R40.1, R40.2, U1.55 (PB6); also elsewhere on the board
/MCU/SPI_MISO: J6.27, R38.1, R38.2, U1.65 (PB4); also elsewhere on the board
/MCU/SPI_MOSI: J6.29, R39.1, R39.2, U1.67 (PB5); also elsewhere on the board
/MCU/SPI_SCK: J6.11, R37.1, R37.2, U1.49 (PA5); also elsewhere on the board
GNDA: J6.9, J6.20, J6.32, J7.8, J7.19, J7.20, J7.22, RV1.1, U1.8 (GND), U1.19 (GND), U1.20 (GND), U1.22 (GND), U1.47 (GND), U1.58 (GND), U1.70 (AGND), U1.77 (GND), U1.78 (GND), U1.79 (GND), U1.80 (GND); also elsewhere on the board
unnamed: R35.2, RV1.2

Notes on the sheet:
Speed Control Input
SPI interface for absolute position motor encoder
CN10 Morpho
OCP Shutdown Trigger
FOC Current sensing
STM32 Nucleo Hookup (Seperate board)
PWM Gate Drive Signals
Header Connectors to STM32
CN7 Morpho

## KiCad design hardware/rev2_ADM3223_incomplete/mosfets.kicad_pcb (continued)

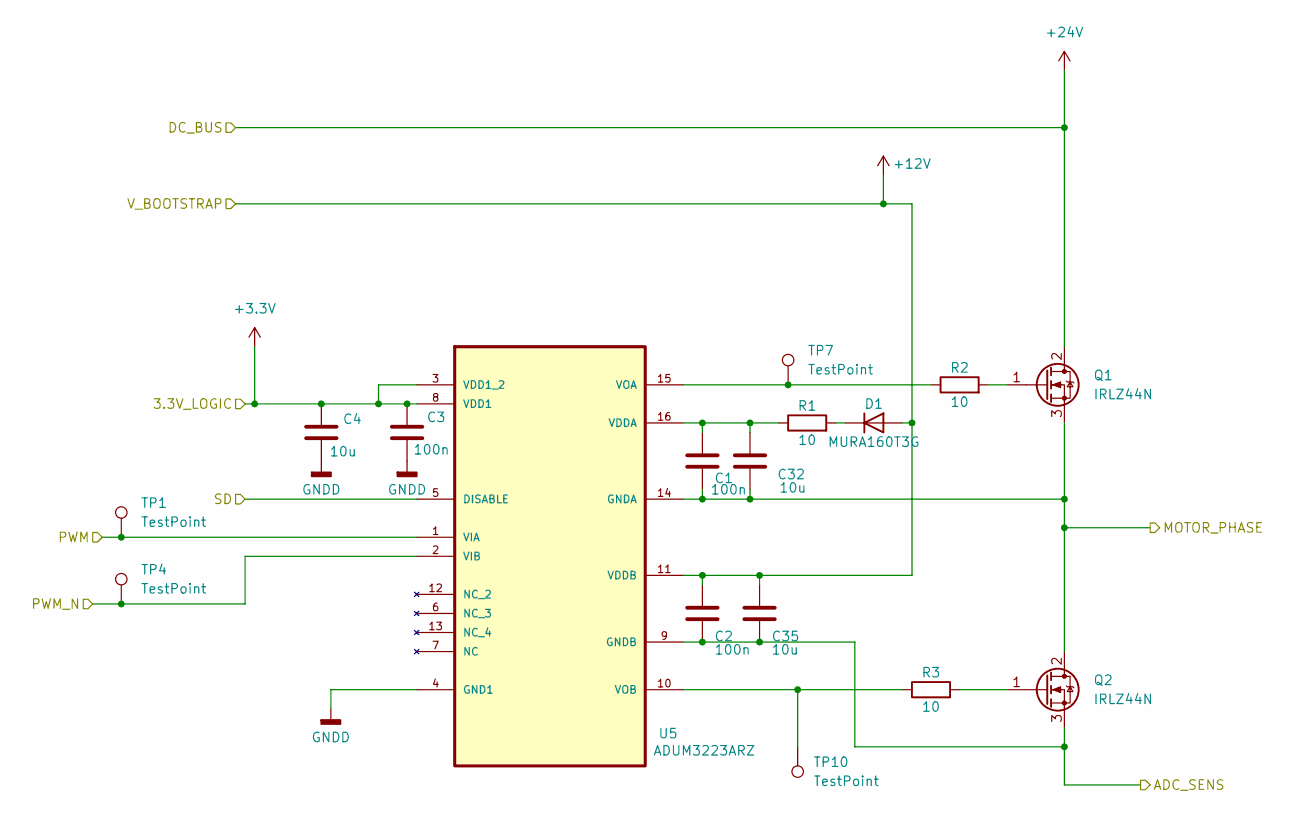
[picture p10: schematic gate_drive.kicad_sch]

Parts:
C1, C2: 100n; C_0805_2012Metric
C3: 100n; C_0603_1608Metric
C4: 10u; C_0603_1608Metric
C32, C35: 10u; C_0805_2012Metric
D1: MURA160T3G
Q1, Q2: IRLZ44N; TO-220-3_Vertical
R1, R2, R3: 10; R_0603_1608Metric
TP1, TP4, TP7, TP10: TestPoint; TestPoint_Pad_D1.5mm
U5: ADUM3223ARZ; SOIC127P600X175-16N; MPN ADUM3223ARZ

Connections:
+3.3V: C3.1, C4.1, U5.3 (VDD1_2), U5.8 (VDD1); also elsewhere on the board
+12V: C2.1, C35.1, D1.2 (A), U5.11 (VDDB); also elsewhere on the board
+24V: Q1.2 (D); also elsewhere on the board
/MCU/PWMN_A: TP4.1 (1_1), U5.2 (VIB); also elsewhere on the board
/MCU/PWM_A: TP1.1 (1_1), U5.1 (VIA); also elsewhere on the board
/OCP_Current_Sens/VSHUNT_A_P: C2.2, C35.2, Q2.3 (S), U5.9 (GNDB); also elsewhere on the board
/PHASE_A: C1.2, C32.2, Q1.3 (S), Q2.2 (D), U5.14 (GNDA); also elsewhere on the board
/SD_A: U5.5 (DISABLE); also elsewhere on the board
GNDA: C3.2, C4.2, U5.4 (GND1); also elsewhere on the board
unnamed: D1.1 (K), R1.2
unnamed: Q1.1 (G), R2.2
unnamed: Q2.1 (G), R3.2
unnamed: C1.1, C32.1, R1.1, U5.16 (VDDA)

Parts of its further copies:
C5, C9: 10u; C_0603_1608Metric
C6, C10: 100n; C_0603_1608Metric
C7, C8, C11, C12: 100n; C_0805_2012Metric
C33, C34, C36, C37: 10u; C_0805_2012Metric
D2, D3: MURA160T3G
Q3, Q4, Q5, Q6: IRLZ44N; TO-220-3_Vertical
R6, R7, R8, R10, R11, R12: 10; R_0603_1608Metric
TP2, TP3, TP5, TP6, TP8, TP9, TP11, TP12: TestPoint; TestPoint_Pad_D1.5mm
U6, U7: ADUM3223ARZ; SOIC127P600X175-16N; MPN ADUM3223ARZ

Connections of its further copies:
+3.3V: C5.1, C6.1, C9.1, C10.1, U6.3 (VDD1_2), U6.8 (VDD1), U7.3 (VDD1_2), U7.8 (VDD1); also elsewhere on the board
+12V: C8.1, C12.1, C36.1, C37.1, D2.2 (A), D3.2 (A), U6.11 (VDDB), U7.11 (VDDB); also elsewhere on the board
+24V: Q3.2 (D), Q5.2 (D); also elsewhere on the board
/MCU/PWMN_B: TP5.1 (1_1), U6.2 (VIB); also elsewhere on the board
/MCU/PWMN_C: TP6.1 (1_1), U7.2 (VIB); also elsewhere on the board
/MCU/PWM_B: TP2.1 (1_1), U6.1 (VIA); also elsewhere on the board
/MCU/PWM_C: TP3.1 (1_1), U7.1 (VIA); also elsewhere on the board
/PHASE_B: C7.2, C33.2, Q3.3 (S), Q4.2 (D), U6.14 (GNDA); also elsewhere on the board
/PHASE_C: C11.2, C34.2, Q5.3 (S), Q6.2 (D), U7.14 (GNDA); also elsewhere on the board
/SD_B: U6.5 (DISABLE); also elsewhere on the board
/SD_C: U7.5 (DISABLE); also elsewhere on the board
GNDA: C5.2, C6.2, C9.2, C10.2, U6.4 (GND1), U7.4 (GND1); also elsewhere on the board
unnamed: D2.1 (K), R6.2
unnamed: D3.1 (K), R10.2
unnamed: Q3.1 (G), R8.2
unnamed: Q4.1 (G), R7.2
unnamed: Q5.1 (G), R12.2
unnamed: Q6.1 (G), R11.2
unnamed: C7.1, C33.1, R6.1, U6.16 (VDDA)
unnamed: R8.1, TP8.1 (1_1), U6.15 (VOA)
unnamed: R7.1, TP11.1 (1_1), U6.10 (VOB)
unnamed: C11.1, C34.1, R10.1, U7.16 (VDDA)

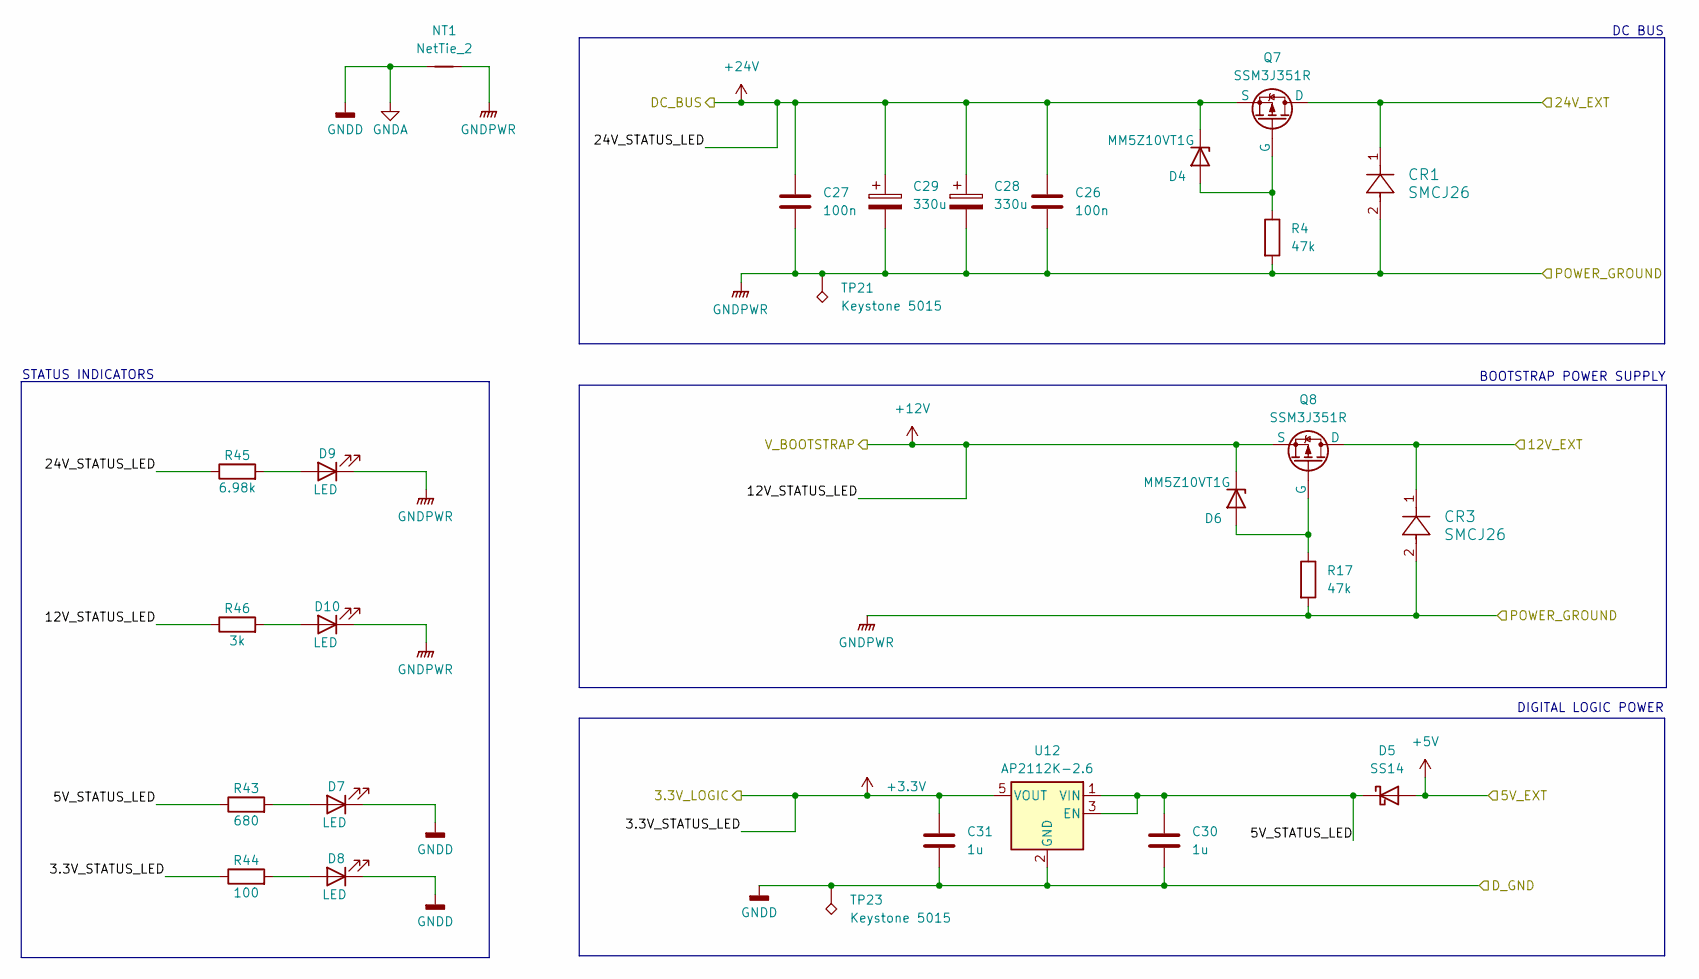
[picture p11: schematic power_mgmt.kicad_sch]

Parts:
C26, C27: 100n; C_0603_1608Metric
C28, C29: 330u; PCAP_12_5x20-THRU-ELECT_NCA
C30, C31: 1u; C_0603_1608Metric
CR1, CR3: SMCJ26; SMCJSeries_LTF
D4, D6: MM5Z10VT1G; D_SOD-523
D5: SS14; D_SMA
D7, D8, D9, D10: LED; LED_0603_1608Metric
NT1: NetTie_2
Q7, Q8: SSM3J351R
R4, R17: 47k; R_0603_1608Metric
R43: 680; R_0603_1608Metric
R44: 100; R_0603_1608Metric
R45: 6.98k; R_1206_3216Metric
R46: 3k; R_0805_2012Metric
TP21, TP23: Keystone 5015; TestPoint_Keystone_5015_Micro_Mini
U12: AP2112K-2.6; SOT-23-5

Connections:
+3.3V: C31.1, R44.1, U12.5 (VOUT); also elsewhere on the board
+5V: D5.2 (A); also elsewhere on the board
+12V: D6.1 (K), Q8.3 (S), R46.1; also elsewhere on the board
+24V: C26.1, C27.1, C28.1, C29.1, D4.1 (K), Q7.3 (S), R45.1; also elsewhere on the board
/Power Management/5V_STATUS_LED: C30.1, D5.1 (K), R43.1, U12.1 (VIN), U12.3 (EN)
/Power Management/12V_EXT: CR3.1, Q8.1 (D); also elsewhere on the board
/Power Management/24V_EXT: CR1.1, Q7.1 (D); also elsewhere on the board
GNDA: C30.2, C31.2, D7.1 (K), D8.1 (K), NT1.1, TP23.1, U12.2 (GND); also elsewhere on the board
GNDPWR: C26.2, C27.2, C28.2, C29.2, CR1.2, CR3.2, D9.1 (K), D10.1 (K), NT1.2, R4.2, R17.2, TP21.1 (1_1); also elsewhere on the board
unnamed: D4.2 (A), Q7.2 (G), R4.1
unnamed: D6.2 (A), Q8.2 (G), R17.1
unnamed: D7.2 (A), R43.2
unnamed: D8.2 (A), R44.2
unnamed: D9.2 (A), R45.2
unnamed: D10.2 (A), R46.2

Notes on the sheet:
BOOTSTRAP POWER SUPPLY
STATUS INDICATORS
DC BUS
DIGITAL LOGIC POWER

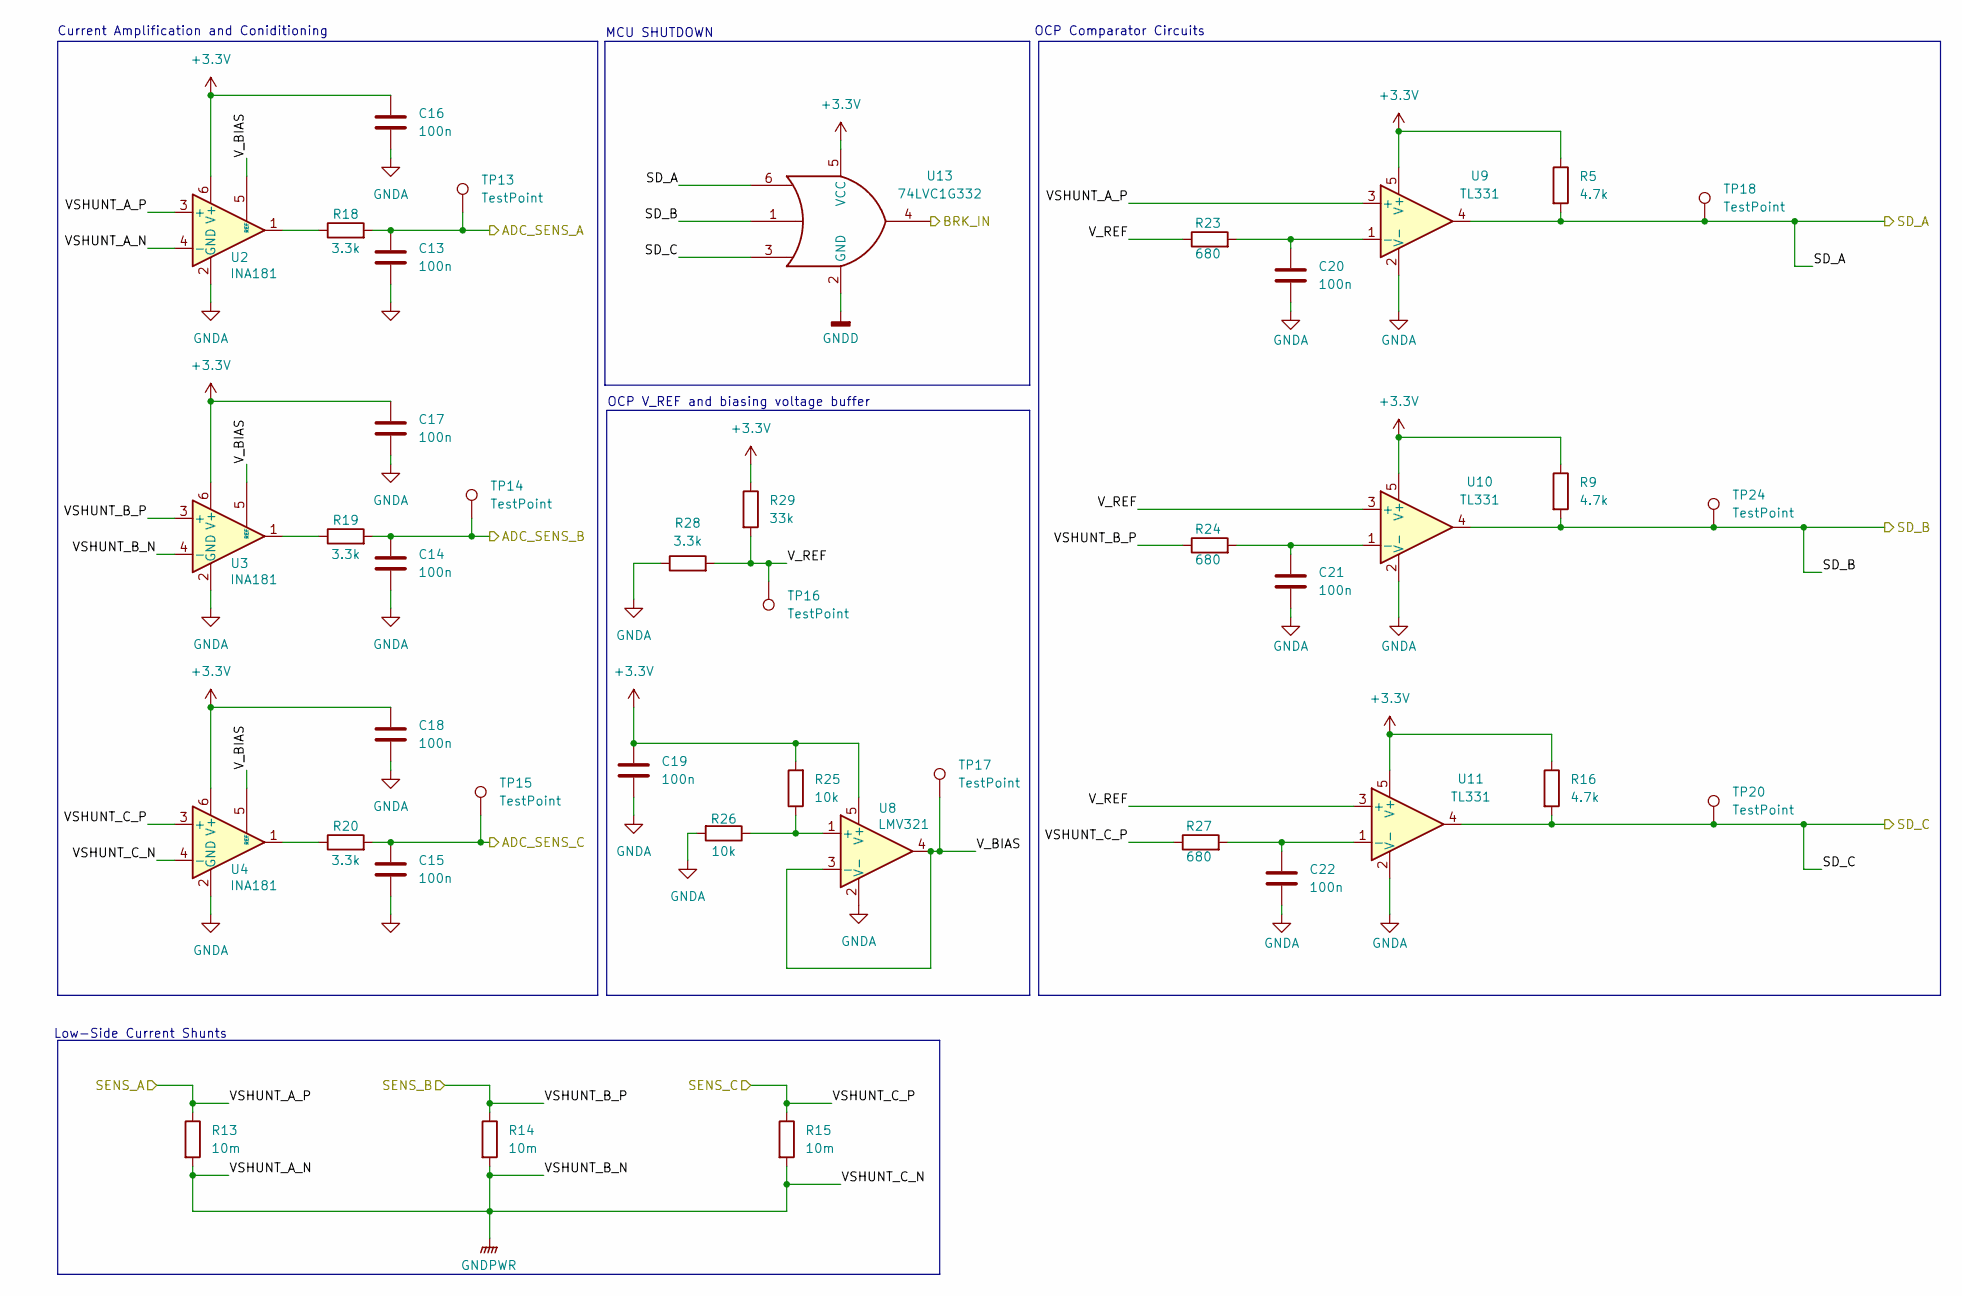
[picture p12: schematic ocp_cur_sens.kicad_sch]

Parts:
C13, C14, C15, C16, C17, C18, C19, C20, C21, C22: 100n; C_0603_1608Metric
R5, R9, R16: 4.7k; R_0603_1608Metric
R13, R14, R15: 10m; R_2512_6332Metric
R18, R19, R20, R28: 3.3k; R_0603_1608Metric
R23, R24, R27: 680; R_0603_1608Metric
R25, R26: 10k; R_0603_1608Metric
R29: 33k; R_0603_1608Metric
TP13, TP14, TP15, TP16, TP17, TP18, TP20: TestPoint; TestPoint_Pad_D1.5mm
TP24: TestPoint; TestPoint_Pad_1.5x1.5mm
U2, U3, U4: INA181; SOT-23-6
U8: LMV321; LMV321DBV5
U9, U10, U11: TL331; SOT-23-5
U13: 74LVC1G332; 74LVC1G332_DCK0006A_N

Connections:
+3.3V: C16.1, C17.1, C18.1, C19.1, R5.1, R9.1, R16.1, R25.2, R29.1, U2.6 (V+), U3.6 (V+), U4.6 (V+), U8.5 (V+), U9.5 (V+), U10.5 (V+), U11.5 (V+), U13.5 (VCC); also elsewhere on the board
/ADC_SENS_A: C13.1, R18.2, TP13.1 (1_1); also elsewhere on the board
/ADC_SENS_B: C14.1, R19.2, TP14.1 (1_1); also elsewhere on the board
/ADC_SENS_C: C15.1, R20.2, TP15.1 (1_1); also elsewhere on the board
/BRK_IN: U13.4; also elsewhere on the board
/OCP_Current_Sens/VSHUNT_A_P: R13.1, U2.3 (+), U9.3 (+); also elsewhere on the board
/OCP_Current_Sens/V_BIAS: TP17.1 (1_1), U2.5 (REF), U3.5 (REF), U4.5 (REF), U8.3 (-), U8.4
/SD_A: R5.2, TP18.1 (1_1), U9.4, U13.6; also elsewhere on the board
/SD_B: R9.2, TP24.1 (1_1), U10.4, U13.1; also elsewhere on the board
/SD_C: R16.2, TP20.1 (1_1), U11.4, U13.3; also elsewhere on the board
GNDA: C13.2, C14.2, C15.2, C16.2, C17.2, C18.2, C19.2, C20.2, C21.2, C22.2, R26.2, R28.1, U2.2 (GND), U3.2 (GND), U4.2 (GND), U8.2 (V-), U9.2 (V-), U10.2 (V-), U11.2 (V-), U13.2 (GND); also elsewhere on the board
GNDPWR: R13.2, R14.2, R15.2, U2.4 (-), U3.4 (-), U4.4 (-); also elsewhere on the board
unnamed: R18.1, U2.1
unnamed: R19.1, U3.1
unnamed: R20.1, U4.1
unnamed: R25.1, R26.1, U8.1 (+)
unnamed: C20.1, R23.2, U9.1 (-)
unnamed: C21.1, R24.2, U10.1 (-)
unnamed: C22.1, R27.2, U11.1 (-)

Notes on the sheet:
Current Amplification and Coniditioning
OCP V_REF and biasing voltage buffer
MCU SHUTDOWN
Low-Side Current Shunts
OCP Comparator Circuits

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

Board: 4 copper layers, 139 parts (1 on the bottom side), 67 nets.

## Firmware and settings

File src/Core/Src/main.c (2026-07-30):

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
/* Includes ------------------------------------------------------------------*/
#include "main.h"
#include "adc.h"
#include "dma.h"
#include "spi.h"
#include "tim.h"
#include "usart.h"
#include "gpio.h"

/* USER CODE BEGIN Includes */
#include "as5048a.h"
#include "sine_lut.h"
#include <stdio.h>
/* USER CODE END Includes */

/* USER CODE BEGIN PD */
#define POT_ADC_MAX        	4095.0f

// calculating Freq hz ===> mechanical rpm * pole pairs / 60
#define FREQ_MIN_HZ         5.0f
#define FREQ_MAX_HZ			85.6f  			// nominal RPM is
#define TIM1_CLOCK_HZ    	168000000.0f 	//set by clock config in stm32, make sure to change if you change the clock speed
/* USER CODE END PD */


/* USER CODE BEGIN PV */

// absolute motor encoder resolver
AS5048A_HandleTypeDef encoder1;

//speed control input potentiometer
volatile uint16_t pot_raw = 0;

/* USER CODE END PV */

void SystemClock_Config(void);
/* USER CODE BEGIN PFP */

void UpdateSpeedFromPot(void);
uint16_t get_pot_val(void);

/* USER CODE END PFP */

/**
  * @brief  The application entry point.
  * @retval int
  */
int main(void)
{

  /* USER CODE BEGIN 1 */
  /* NOTHING TIM1/DMA-related here. htim1 does not exist yet --
   * MX_TIM1_Init() has not run. All PWM/DMA start calls moved to
   * USER CODE BEGIN 2, after every MX_*_Init() has completed. */
  /* USER CODE END 1 */

  /* MCU Configuration--------------------------------------------------------*/

  /* Reset of all peripherals, Initializes the Flash interface and the Systick. */
  HAL_Init();

  /* Configure the system clock */
  SystemClock_Config();

  /* Initialize all configured peripherals */
  MX_GPIO_Init();
  MX_DMA_Init();
  MX_ADC1_Init();
  MX_SPI1_Init();
  MX_TIM1_Init();
  MX_USART2_UART_Init();
  /* USER CODE BEGIN 2 */


  // start the absolute encoder on the motor for feedback loop control
  AS5048A_Init(&encoder1, &hspi1, SPI1_CSn_GPIO_Port, SPI1_CSn_Pin);
  AS5048A_ClearErrorFlag(&encoder1, NULL);

  //this starts up the potentiometer DMA, technically this could be a blocking function in the main loop, but why not free up the CPU for other shit?
  // start the DMA for the potentiometer for speed control setting
  HAL_ADC_Start_DMA(&hadc1, (uint32_t*)&pot_raw, 1);

  // this starts up the DMA's for the sine lookup tables
  //each DMA on each channel corresponds to phase A, B, C
  HAL_StatusTypeDef dma_status;

  dma_status = HAL_TIM_PWM_Start_DMA(&htim1, TIM_CHANNEL_1, (uint32_t*)sine_lut_a, LUT_SIZE);
  if (dma_status != HAL_OK) { Error_Handler(); }

  dma_status = HAL_TIM_PWM_Start_DMA(&htim1, TIM_CHANNEL_2, (uint32_t*)sine_lut_b, LUT_SIZE);
  if (dma_status != HAL_OK) { Error_Handler(); }

  dma_status = HAL_TIM_PWM_Start_DMA(&htim1, TIM_CHANNEL_3, (uint32_t*)sine_lut_c, LUT_SIZE);
  if (dma_status != HAL_OK) { Error_Handler(); }

  HAL_TIMEx_PWMN_Start(&htim1, TIM_CHANNEL_1);
  HAL_TIMEx_PWMN_Start(&htim1, TIM_CHANNEL_2);
  HAL_TIMEx_PWMN_Start(&htim1, TIM_CHANNEL_3);



  /* --code just to see the PWM output with no SPWM or DMA garbage
  __HAL_TIM_SET_COMPARE(&htim1, TIM_CHANNEL_1, 4300);
  __HAL_TIM_SET_COMPARE(&htim1, TIM_CHANNEL_2, 4300);
  __HAL_TIM_SET_COMPARE(&htim1, TIM_CHANNEL_3, 4300);

  HAL_TIM_PWM_Start(&htim1, TIM_CHANNEL_1);
  HAL_TIM_PWM_Start(&htim1, TIM_CHANNEL_2);
  HAL_TIM_PWM_Start(&htim1, TIM_CHANNEL_3);

  */

  /* USER CODE END 2 */

  /* Infinite loop */
  /* USER CODE BEGIN WHILE */
  AS5048A_AngleTypeDef angle;

  while (1)
  {




	/*
    if (AS5048A_ReadAngle(&encoder1, &angle))
    {
      if (!angle.parity_ok)
      {
        printf("AS5048A: parity error, discarding sample\r\n");
      }
      else
      {
        printf("raw=%5u  angle=%7.2f deg  err_flag=%d\r\n",
               angle.raw_angle, angle.angle_deg, angle.error_flag);
      }
    }
    else
    {
      printf("AS5048A: SPI transfer failed (check wiring/CS pin)\r\n");
    }
	*/
	//pot_raw = get_pot_val();
    //UpdateSpeedFromPot();

    HAL_Delay(100);



    /* USER CODE END WHILE */

    /* USER CODE BEGIN 3 */
  }
  /* USER CODE END 3 */
}

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
/* USER CODE BEGIN 4 */
#ifdef __GNUC__
int _write(int file, char *ptr, int len)
{
    HAL_UART_Transmit(&huart2, (uint8_t *)ptr, len, HAL_MAX_DELAY);
    return len;
}
#endif

uint16_t get_pot_val(void)
{
    HAL_ADC_Start(&hadc1);
    HAL_ADC_PollForConversion(&hadc1, 10);
    uint16_t val = HAL_ADC_GetValue(&hadc1);
    HAL_ADC_Stop(&hadc1);
    return val;
}

void UpdateSpeedFromPot(void) {

	float pot_frac = pot_raw / POT_ADC_MAX;
	float target_freq_hz = FREQ_MIN_HZ + pot_frac * (FREQ_MAX_HZ - FREQ_MIN_HZ);
	float update_rate_hz = target_freq_hz * LUT_SIZE;

	//we basically are manipulating the prescalar value in TIM1 as a way to manipulate the speed in which we step through the LUT
	uint32_t new_psc = (uint32_t)(TIM1_CLOCK_HZ /
	                    (update_rate_hz * (htim1.Init.Period + 1) * 2)) - 1;

	//if the register on the ADC is fucked up, just default to
	if (new_psc > 65535) {
		new_psc = 65535;
	}

	__HAL_TIM_SET_PRESCALER(&htim1, new_psc);
}

/* USER CODE END 4 */
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


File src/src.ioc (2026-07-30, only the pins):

Mcu.UserName=STM32F446RETx
PA1.Signal=ADCx_IN1
PA10.Signal=S_TIM1_CH3
PA13.GPIO_Label=T_SWDIO
PA13.Signal=SYS_JTMS-SWDIO
PA14.GPIO_Label=T_SWCLK
PA14.Signal=SYS_JTCK-SWCLK
PA2.Signal=USART2_TX
PA3.Signal=USART2_RX
PA4.GPIO_Label=SPI1_CSn
PA4.Signal=GPIO_Output
PA5.Signal=SPI1_SCK
PA7.Signal=TIM1_CH1N
PA8.Signal=S_TIM1_CH1
PA9.Signal=S_TIM1_CH2
PB0.Signal=TIM1_CH2N
PB1.Signal=TIM1_CH3N
PB3.GPIO_Label=T_SWO
PB3.Signal=SYS_JTDO-SWO
PB4.Signal=SPI1_MISO
PB5.Signal=SPI1_MOSI
PH0-OSC_IN.Signal=RCC_OSC_IN
PH1-OSC_OUT.Signal=RCC_OSC_OUT

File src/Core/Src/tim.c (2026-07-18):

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
/* Includes ------------------------------------------------------------------*/
#include "tim.h"

TIM_HandleTypeDef htim1;
DMA_HandleTypeDef hdma_tim1_ch1;
DMA_HandleTypeDef hdma_tim1_ch2;
DMA_HandleTypeDef hdma_tim1_ch3;

/* TIM1 init function */
void MX_TIM1_Init(void)
{

  TIM_ClockConfigTypeDef sClockSourceConfig = {0};
  TIM_MasterConfigTypeDef sMasterConfig = {0};
  TIM_OC_InitTypeDef sConfigOC = {0};
  TIM_BreakDeadTimeConfigTypeDef sBreakDeadTimeConfig = {0};

  htim1.Instance = TIM1;
  htim1.Init.Prescaler = 0;
  htim1.Init.CounterMode = TIM_COUNTERMODE_CENTERALIGNED1;
  htim1.Init.Period = 8599;
  htim1.Init.ClockDivision = TIM_CLOCKDIVISION_DIV1;
  htim1.Init.RepetitionCounter = 1;
  htim1.Init.AutoReloadPreload = TIM_AUTORELOAD_PRELOAD_DISABLE;
  if (HAL_TIM_Base_Init(&htim1) != HAL_OK)
  {
    Error_Handler();
  }
  sClockSourceConfig.ClockSource = TIM_CLOCKSOURCE_INTERNAL;
  if (HAL_TIM_ConfigClockSource(&htim1, &sClockSourceConfig) != HAL_OK)
  {
    Error_Handler();
  }
  if (HAL_TIM_PWM_Init(&htim1) != HAL_OK)
  {
    Error_Handler();
  }
  sMasterConfig.MasterOutputTrigger = TIM_TRGO_RESET;
  sMasterConfig.MasterSlaveMode = TIM_MASTERSLAVEMODE_DISABLE;
  if (HAL_TIMEx_MasterConfigSynchronization(&htim1, &sMasterConfig) != HAL_OK)
  {
    Error_Handler();
  }
  sConfigOC.OCMode = TIM_OCMODE_PWM1;
  sConfigOC.Pulse = 1;
  sConfigOC.OCPolarity = TIM_OCPOLARITY_HIGH;
  sConfigOC.OCNPolarity = TIM_OCNPOLARITY_HIGH;
  sConfigOC.OCFastMode = TIM_OCFAST_DISABLE;
  sConfigOC.OCIdleState = TIM_OCIDLESTATE_RESET;
  sConfigOC.OCNIdleState = TIM_OCNIDLESTATE_RESET;
  if (HAL_TIM_PWM_ConfigChannel(&htim1, &sConfigOC, TIM_CHANNEL_1) != HAL_OK)
  {
    Error_Handler();
  }
  if (HAL_TIM_PWM_ConfigChannel(&htim1, &sConfigOC, TIM_CHANNEL_2) != HAL_OK)
  {
    Error_Handler();
  }
  if (HAL_TIM_PWM_ConfigChannel(&htim1, &sConfigOC, TIM_CHANNEL_3) != HAL_OK)
  {
    Error_Handler();
  }
  sBreakDeadTimeConfig.OffStateRunMode = TIM_OSSR_ENABLE;
  sBreakDeadTimeConfig.OffStateIDLEMode = TIM_OSSI_ENABLE;
  sBreakDeadTimeConfig.LockLevel = TIM_LOCKLEVEL_OFF;
  sBreakDeadTimeConfig.DeadTime = 100;
  sBreakDeadTimeConfig.BreakState = TIM_BREAK_DISABLE;
  sBreakDeadTimeConfig.BreakPolarity = TIM_BREAKPOLARITY_HIGH;
  sBreakDeadTimeConfig.AutomaticOutput = TIM_AUTOMATICOUTPUT_ENABLE;
  if (HAL_TIMEx_ConfigBreakDeadTime(&htim1, &sBreakDeadTimeConfig) != HAL_OK)
  {
    Error_Handler();
  }
  HAL_TIM_MspPostInit(&htim1);

}

void HAL_TIM_Base_MspInit(TIM_HandleTypeDef* tim_baseHandle)
{

  if(tim_baseHandle->Instance==TIM1)
  {
    /* TIM1 clock enable */
    __HAL_RCC_TIM1_CLK_ENABLE();

    /* TIM1 DMA Init */
    /* TIM1_CH1 Init */
    hdma_tim1_ch1.Instance = DMA2_Stream1;
    hdma_tim1_ch1.Init.Channel = DMA_CHANNEL_6;
    hdma_tim1_ch1.Init.Direction = DMA_MEMORY_TO_PERIPH;
    hdma_tim1_ch1.Init.PeriphInc = DMA_PINC_DISABLE;
    hdma_tim1_ch1.Init.MemInc = DMA_MINC_ENABLE;
    hdma_tim1_ch1.Init.PeriphDataAlignment = DMA_PDATAALIGN_HALFWORD;
    hdma_tim1_ch1.Init.MemDataAlignment = DMA_MDATAALIGN_HALFWORD;
    hdma_tim1_ch1.Init.Mode = DMA_CIRCULAR;
    hdma_tim1_ch1.Init.Priority = DMA_PRIORITY_HIGH;
    hdma_tim1_ch1.Init.FIFOMode = DMA_FIFOMODE_DISABLE;
    if (HAL_DMA_Init(&hdma_tim1_ch1) != HAL_OK)
    {
      Error_Handler();
    }

    __HAL_LINKDMA(tim_baseHandle,hdma[TIM_DMA_ID_CC1],hdma_tim1_ch1);

    /* TIM1_CH2 Init */
    hdma_tim1_ch2.Instance = DMA2_Stream2;
    hdma_tim1_ch2.Init.Channel = DMA_CHANNEL_6;
    hdma_tim1_ch2.Init.Direction = DMA_MEMORY_TO_PERIPH;
    hdma_tim1_ch2.Init.PeriphInc = DMA_PINC_DISABLE;
    hdma_tim1_ch2.Init.MemInc = DMA_MINC_ENABLE;
    hdma_tim1_ch2.Init.PeriphDataAlignment = DMA_PDATAALIGN_HALFWORD;
    hdma_tim1_ch2.Init.MemDataAlignment = DMA_MDATAALIGN_HALFWORD;
    hdma_tim1_ch2.Init.Mode = DMA_CIRCULAR;
    hdma_tim1_ch2.Init.Priority = DMA_PRIORITY_HIGH;
    hdma_tim1_ch2.Init.FIFOMode = DMA_FIFOMODE_DISABLE;
    if (HAL_DMA_Init(&hdma_tim1_ch2) != HAL_OK)
    {
      Error_Handler();
    }

    __HAL_LINKDMA(tim_baseHandle,hdma[TIM_DMA_ID_CC2],hdma_tim1_ch2);

    /* TIM1_CH3 Init */
    hdma_tim1_ch3.Instance = DMA2_Stream6;
    hdma_tim1_ch3.Init.Channel = DMA_CHANNEL_6;
    hdma_tim1_ch3.Init.Direction = DMA_MEMORY_TO_PERIPH;
    hdma_tim1_ch3.Init.PeriphInc = DMA_PINC_DISABLE;
    hdma_tim1_ch3.Init.MemInc = DMA_MINC_ENABLE;
    hdma_tim1_ch3.Init.PeriphDataAlignment = DMA_PDATAALIGN_HALFWORD;
    hdma_tim1_ch3.Init.MemDataAlignment = DMA_MDATAALIGN_HALFWORD;
    hdma_tim1_ch3.Init.Mode = DMA_CIRCULAR;
    hdma_tim1_ch3.Init.Priority = DMA_PRIORITY_HIGH;
    hdma_tim1_ch3.Init.FIFOMode = DMA_FIFOMODE_DISABLE;
    if (HAL_DMA_Init(&hdma_tim1_ch3) != HAL_OK)
    {
      Error_Handler();
    }

    __HAL_LINKDMA(tim_baseHandle,hdma[TIM_DMA_ID_CC3],hdma_tim1_ch3);

  }
}
void HAL_TIM_MspPostInit(TIM_HandleTypeDef* timHandle)
{

  GPIO_InitTypeDef GPIO_InitStruct = {0};
  if(timHandle->Instance==TIM1)
  {
    __HAL_RCC_GPIOA_CLK_ENABLE();
    __HAL_RCC_GPIOB_CLK_ENABLE();
    /**TIM1 GPIO Configuration
    PA7     ------> TIM1_CH1N
    PB0     ------> TIM1_CH2N
    PB1     ------> TIM1_CH3N
    PA8     ------> TIM1_CH1
    PA9     ------> TIM1_CH2
    PA10     ------> TIM1_CH3
    */
    GPIO_InitStruct.Pin = GPIO_PIN_7|GPIO_PIN_8|GPIO_PIN_9|GPIO_PIN_10;
    GPIO_InitStruct.Mode = GPIO_MODE_AF_PP;
    GPIO_InitStruct.Pull = GPIO_NOPULL;
    GPIO_InitStruct.Speed = GPIO_SPEED_FREQ_LOW;
    GPIO_InitStruct.Alternate = GPIO_AF1_TIM1;
    HAL_GPIO_Init(GPIOA, &GPIO_InitStruct);

    GPIO_InitStruct.Pin = GPIO_PIN_0|GPIO_PIN_1;
    GPIO_InitStruct.Mode = GPIO_MODE_AF_PP;
    GPIO_InitStruct.Pull = GPIO_NOPULL;
    GPIO_InitStruct.Speed = GPIO_SPEED_FREQ_LOW;
    GPIO_InitStruct.Alternate = GPIO_AF1_TIM1;
    HAL_GPIO_Init(GPIOB, &GPIO_InitStruct);

  }

}

void HAL_TIM_Base_MspDeInit(TIM_HandleTypeDef* tim_baseHandle)
{

  if(tim_baseHandle->Instance==TIM1)
  {
    /* Peripheral clock disable */
    __HAL_RCC_TIM1_CLK_DISABLE();

    /* TIM1 DMA DeInit */
    HAL_DMA_DeInit(tim_baseHandle->hdma[TIM_DMA_ID_CC1]);
    HAL_DMA_DeInit(tim_baseHandle->hdma[TIM_DMA_ID_CC2]);
    HAL_DMA_DeInit(tim_baseHandle->hdma[TIM_DMA_ID_CC3]);
  }
}



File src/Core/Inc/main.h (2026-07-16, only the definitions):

#define SPI1_CSn_Pin GPIO_PIN_4
#define SPI1_CSn_GPIO_Port GPIOA
#define T_SWDIO_Pin GPIO_PIN_13
#define T_SWDIO_GPIO_Port GPIOA
#define T_SWCLK_Pin GPIO_PIN_14
#define T_SWCLK_GPIO_Port GPIOA
#define T_SWO_Pin GPIO_PIN_3
#define T_SWO_GPIO_Port GPIOB

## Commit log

2026-04-27 setup inverter electrical circuit
2026-04-29 created schematic file and added stm32 nucleo library
    [inverter_pcb.kicad_pcb, inverter_pcb.kicad_sch]
2026-05-02 added some hardware to git
    [controller.kicad_sch, inverter_bridge.kicad_sch, inverter_pcb.kicad_sch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]
2026-05-04 added decoupling in the mathematical model
    [controller.kicad_sch]
2026-05-22 added hardware
    [controller.kicad_sch, inverter_bridge.kicad_sch, inverter_pcb.kicad_pcb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]
2026-05-25 housekeeping files
    [mosfets.kicad_pcb, mosfets.kicad_sch]
2026-05-28 PWM shoot through current protection model added
2026-06-01 updated alternate design
    [MCU.kicad_sch, gate_drive.kicad_sch, mosfets.kicad_sch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]
2026-06-02 updates to kicad schema
    [MCU.kicad_sch, ocp_cur_sens.kicad_sch, power_mgmt.kicad_sch]
2026-06-03 added OCP
    [MCU.kicad_sch, gate_drive.kicad_sch, mosfets.kicad_sch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]
2026-06-18 major additions to schematic of inverter
    [MCU.kicad_sch, auxaillary_power_supply_current_draw_from_buck_converter.xlsx, gate_drive.kicad_sch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]
2026-06-24 completed project schema
    [MCU.kicad_sch, gate_drive.kicad_sch, mosfets.kicad_pcb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]
2026-06-25 added status LED's to schema, fixed gate drive error, added BOM
    [BOM_no_links.csv, MCU.kicad_sch, gate_drive.kicad_sch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]
2026-06-25 verification of gate driver circuit with proper files
2026-06-27 footprints updated in hardware
    [power_mgmt.kicad_sch]
2026-06-29 hardware layout started
    [MCU.kicad_sch, gate_drive.kicad_sch, mosfets.kicad_pcb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]

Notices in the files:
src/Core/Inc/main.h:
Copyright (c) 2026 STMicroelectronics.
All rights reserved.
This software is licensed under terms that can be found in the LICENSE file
